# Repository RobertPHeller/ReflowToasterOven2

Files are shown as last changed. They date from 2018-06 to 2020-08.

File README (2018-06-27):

This project is based on the Instructables "Hack a Toaster Oven for Reflow
Soldering" by frank26080115 at
https://www.instructables.com/id/Hack-a-Toaster-Oven-for-Reflow-Soldering/

Notable differences:

1) It uses an Adafruit Feather M0 Expressas the processing element and all of
the electronics (except the display, pushbuttons, buzzer, and relay) are
mounted on an cut down BusBoard Prototype Systems BR1 solderable breadboard --
all of the components are through-hole components.

There is a KiCAD project here. It includes a "four layer" board. Actually I
have no intention of creating a "four layer" PCB. I intend to build this on
aBusBoard Prototype Systems BR1 solderable breadboard. The PCB I "designed"
with KiCAD is a mock up for the BR1 solderable breadboard. The green layer
represent the wiring already on the BR1 solderable breadboard, and includes
the bus strips. The red, blue and white "layers" represent the added wiring.
The board also provides the component placement. For those people without
KiCAD installed, I have included a PDF of the schematic in the file
ReflowToasterOven2.pdf and a SVG file of the board showing the layout.

2) Everything is mounted in a pair of plastic boxes and instead of "hacking"
an extension code, an AC power entry module and a pair of AC Receptacles are
used.

There are three files related to the mechanical construction:

ReflowToasterOven-mech2.tcl
ReflowToasterOven-mech2.gcad
ReflowToasterOven-mech2.dxf

ReflowToasterOven-mech2.tcl is a Tcl program that generates the 
ReflowToasterOven-mech2.gcad file, which is the input for the GCAD3D program.  
The ReflowToasterOven-mech2.dxf is a DXF file, that can be imported to any 3D 
cad program.

3) An Adafruit 1.8" *Color* TFT LCD SPI display is used, using Adafruit's 
graphics library.

4) The software is a "standard" Arduino project.

And the code lives in the ReflowToasterOven2 subdirectory. It compiles
successfully and just fits in the Uno's flash memory and only 1/2 of the SRAM
is used by static variables, leaving just under 1K for dynamic variables.

You will need to install the Adafruit ST7735 and Adafruit_GFX libraries from 
Adafruit's GitHub repo.  You will also need the MsTimer2 library 
(http://www.pjrc.com/teensy/td_libs_MsTimer2.html).

*Most* of the code is copied from the original program by frank26080115.  I 
modified things to use C++ classes and adapted to use the Arduino I/O 
libraries, the Adafruit ST7735-based TFT display and the MsTimer2 library.

I have not built or tested it yet.

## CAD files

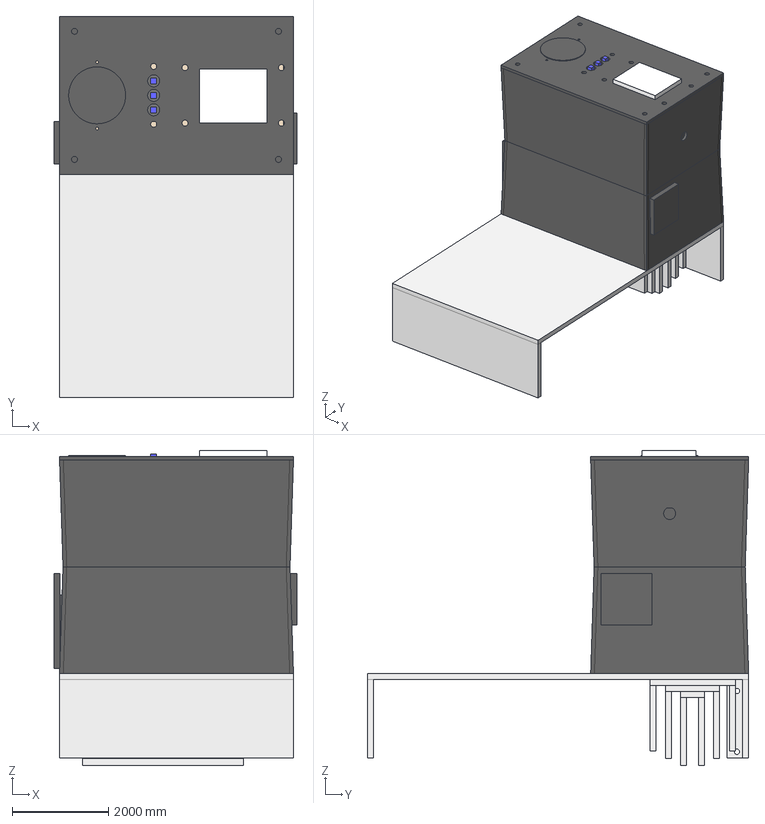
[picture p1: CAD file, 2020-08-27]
ReflowToasterOven.fcstd
5036.1 x 7910.9 x 6534.9 mm
reflowcontrol_upperbox
reflowcontrol_upperbox_lid
reflowcontrol_lowerbox
reflowcontrol_board_board
reflowcontrol_board_h1
reflowcontrol_board_h2
reflowcontrol_board_feather
reflowcontrol_board_usbjack
reflowcontrol_display_board
reflowcontrol_display_display
reflowcontrol_buzzer
reflowcontrol_relay
reflowcontrol_acpowerentry
reflowcontrol_backrecept
reflowcontrol_heatsink_mainpanel
reflowcontrol_heatsink_fin1
reflowcontrol_heatsink_fin2
reflowcontrol_heatsink_fin3
reflowcontrol_buttonboard_board
reflowcontrol_buttonboard_button1_body
reflowcontrol_buttonboard_button1_button
reflowcontrol_buttonboard_button2_body
reflowcontrol_buttonboard_button2_button
reflowcontrol_buttonboard_button3_body
reflowcontrol_buttonboard_button3_button
reflowcontrol_board_standoff1
reflowcontrol_board_standoff2
reflowcontrol_board_standoff3
reflowcontrol_board_standoff4

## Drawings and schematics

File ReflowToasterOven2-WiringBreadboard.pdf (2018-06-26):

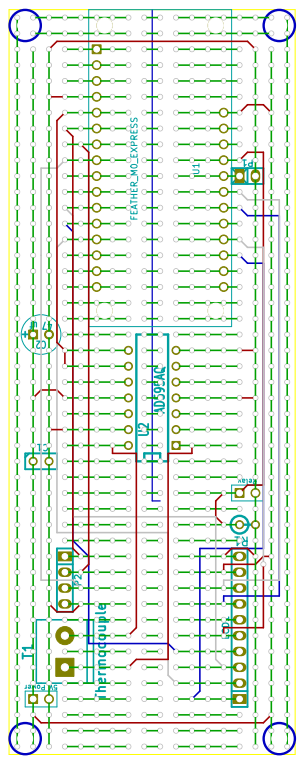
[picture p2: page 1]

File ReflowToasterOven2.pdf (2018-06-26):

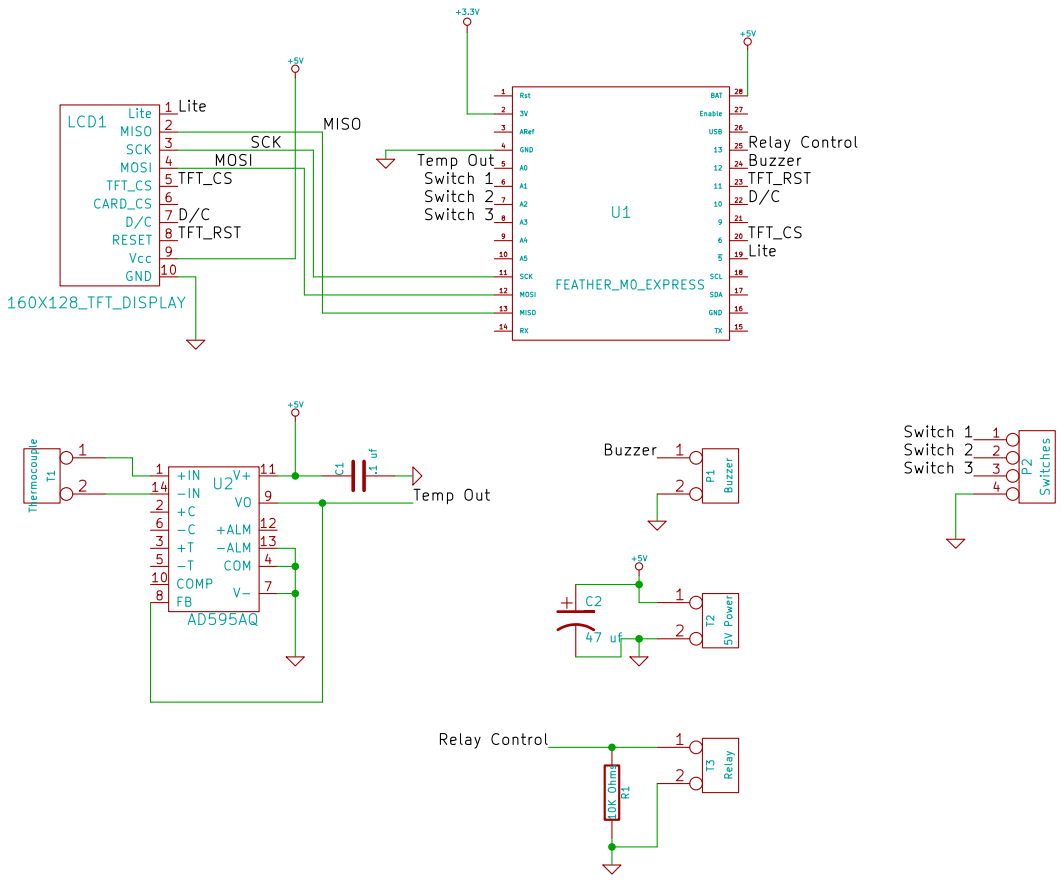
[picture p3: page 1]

Id: 1/1 Title: File: ReflowToasterOven2.sch
Sheet: /

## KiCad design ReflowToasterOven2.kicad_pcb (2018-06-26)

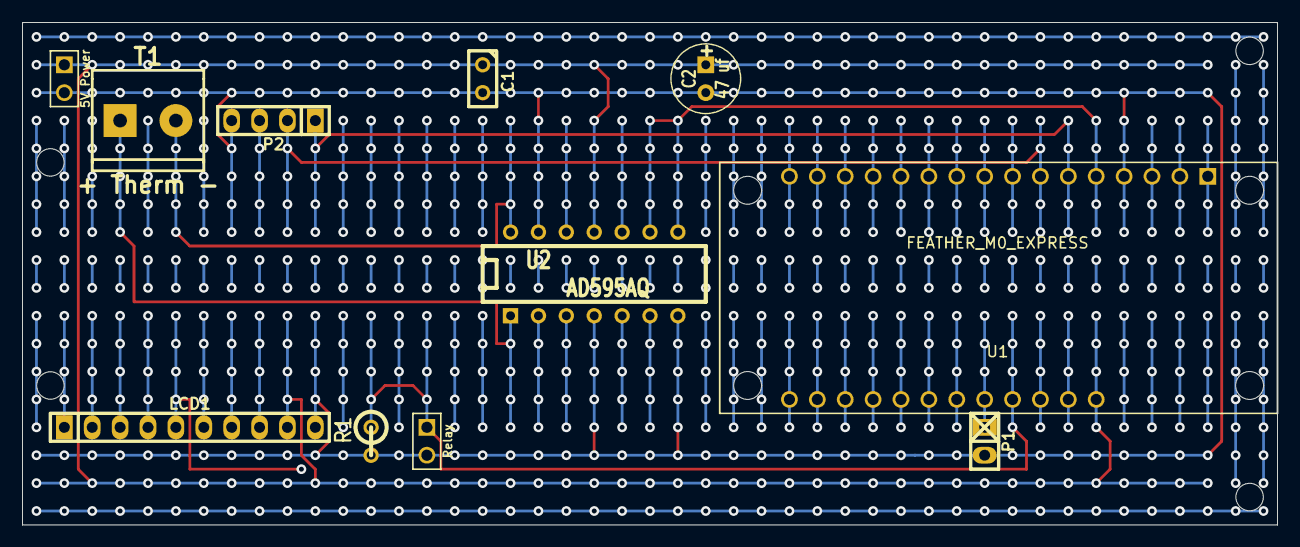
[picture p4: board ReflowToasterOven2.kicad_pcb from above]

Board: 4 copper layers, 114.3 x 45.8 mm, 15 parts (0 on the bottom side), 17 nets.

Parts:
C1: .1 uf; C1
C2: 47 uf; C1V7
LCD1: 160X128_TFT_DISPLAY; pin_strip_10
MH: MountingHole_2-5mm_RevA_Date21Jun2010
MH#2, MH#3, MH#4: MountingHole_2-5mm_RevA_Date21Jun2010
P1: Buzzer; pin_strip_2
P2: Switches; pin_strip_4
R1: 10K Ohms; R1
T1: + Therm -; mors_2p
T2: 5V Power; ScrewTerm2.54-2
T3: Relay; ScrewTerm2.54-2
U1: FEATHER_M0_EXPRESS; AdafruitFeather
U2: AD595AQ; DIP-14__300

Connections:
+5V: C1.1, C2.1, LCD1.9, T2.1, U1.28, U2.11
/Buzzer: P1.1, U1.24
/D/C: LCD1.7, U1.22
/Lite: LCD1.1, U1.19
/MISO: LCD1.2, U1.13
/MOSI: LCD1.4, U1.12
/Relay Control: R1.1, T3.1, U1.25
/SCK: LCD1.3, U1.11
/Switch 1: P2.1, U1.6
/Switch 2: P2.2, U1.7
/Switch 3: P2.3, U1.8
/TFT_CS: LCD1.5, U1.20
/TFT_RST: LCD1.8, U1.23
/Temp Out: U1.5, U2.8, U2.9
GND: C1.2, C2.2, LCD1.10, P1.2, P2.4, R1.2, T2.2, T3.2, U1.4, U2.4, U2.7, U2.13
unnamed: T1.1, U2.1
unnamed: T1.2, U2.14

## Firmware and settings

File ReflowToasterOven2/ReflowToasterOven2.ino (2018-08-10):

// -!- C++ -!- //////////////////////////////////////////////////////////////
//
//  System        : 
//  Module        : 
//  Object Name   : $RCSfile$
//  Revision      : $Revision$
//  Date          : $Date$
//  Author        : $Author$
//  Created By    : Robert Heller
//  Created       : Sun Jun 24 09:38:54 2018
//  Last Modified : <180810.0919>
//
//  Description	
//
//  Notes
//
//  History
//	
/////////////////////////////////////////////////////////////////////////////
//
//    Copyright (C) 2018  Robert Heller D/B/A Deepwoods Software
//			51 Locke Hill Road
//			Wendell, MA 01379-9728
//
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
// 
//
//////////////////////////////////////////////////////////////////////////////
#include <Arduino.h>
#include <stdio.h>
//#include <EEPROM.h>

#include <Adafruit_GFX.h>
#include <Adafruit_ST7735.h>
#include <SPI.h>
#include <Adafruit_SPIFlash.h>
#include <Adafruit_SPIFlash_FatFs.h>
#include <Adafruit_ZeroTimer.h>
#include "reflowtoasteroven.h"
#include "temperaturemeasurement.h"
#include "heatingelement.h"
#include "Menu.h"
#include "FileIO.h"
#include "pitches.h"

static const char rcsid[] = "@(#) : $Id$";

settings_t settings; // store this globally so it's easy to access

FileIO filesystem;

void tmr_init();

Adafruit_ZeroTimer zt4 = Adafruit_ZeroTimer(4);


Menu menu = Menu();
TemperatureMeasurement sensor = TemperatureMeasurement();
Heat element = Heat();

void setup()
{
    Serial.begin(115200);
    Serial.println("Initializing...");
    
    filesystem.begin();
    sensor.init();
    element.init();
#ifdef TIMER
    tmr_init();
#endif
    menu.init();
    Serial.println("Reflow Toaster Oven 1.0 Setup finished");
    menu.main();
}

volatile uint16_t tmr_ovf_cnt = 0;
volatile char tmr_checktemp_flag = 0;
volatile char tmr_drawlcd_flag = 0;
volatile char tmr_writelog_flag = 0;

void loop() {
    if (Serial.available() > 0) {
        while (Serial.available() > 0 && Serial.read() != '\n') ;
        Serial.print("*** tmr_ovf_cnt = ");Serial.println(tmr_ovf_cnt);
        Serial.print("*** tmr_checktemp_flag = ");Serial.println(tmr_checktemp_flag);
        Serial.print("*** tmr_drawlcd_flag = ");Serial.println(tmr_drawlcd_flag);
        Serial.print("*** tmr_writelog_flag = ");Serial.println(tmr_writelog_flag);
        //menu.fillRect(0,0,50,50,ST7735_BLUE);
        //tone(BUZZER,NOTE_GS3,3000);
        delay(1000);
    } else {
        //menu.fillRect(25,25,25,24,ST7735_RED);
    }
#if 0
    if (button_up()) {
        button_debounce();
        while (button_up());
        button_debounce();
        Serial.println("Button up");
    } else if (button_mid()) {
        button_debounce();
        while (button_mid());
        button_debounce();
        Serial.println("Button mid");
    } else if (button_down()) {
        button_debounce();
        while (button_down());
        button_debounce();
        Serial.println("Button down");
    }
#endif
    delay(1);
} // Not used

void TIMER0_OVF_vect()
{
    element.isr();
    sensor.get_ADC_sample();
    
    tmr_ovf_cnt++;
    if (tmr_ovf_cnt % 1024 == 0) //  2s
    {
        tmr_ovf_cnt = 0;
        tmr_checktemp_flag = 1;
        tmr_drawlcd_flag = 1;
        tmr_writelog_flag = 1;
    }
    else if (tmr_ovf_cnt % 512 == 0) //  1s
    {
        tmr_checktemp_flag = 1;
        tmr_writelog_flag = 1;
    }
    else if (tmr_ovf_cnt % 256 == 0) //  0.5s
    {
        tmr_checktemp_flag = 1;
    }
}

void tmr_init()
{
    /********************* Timer #4, 8 bit, one callback with adjustable period */
    zt4.configure(TC_CLOCK_PRESCALER_DIV64, // prescaler: 48Mhz/64 = 750Khz
                  TC_COUNTER_SIZE_16BIT,   // bit width of timer/counter
                  TC_WAVE_GENERATION_MATCH_FREQ  // match style
                  );
    
    zt4.setPeriodMatch(1464, 1, 0); // 1 match, channel 0 -- 1.953125ms (512Hz == 750Khz/1464)
    zt4.setCallback(true, TC_CALLBACK_CC_CHANNEL0, TIMER0_OVF_vect); 
    zt4.enable(true);
}

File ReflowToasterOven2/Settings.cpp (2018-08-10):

// -!- C++ -!- //////////////////////////////////////////////////////////////
//
//  System        : 
//  Module        : 
//  Object Name   : $RCSfile$
//  Revision      : $Revision$
//  Date          : $Date$
//  Author        : $Author$
//  Created By    : Robert Heller
//  Created       : Sat Mar 24 15:41:16 2018
//  Last Modified : <180810.1114>
//
//  Description	
//
//  Notes
//
//  History
//	
/////////////////////////////////////////////////////////////////////////////
//
//    Copyright (C) 2018  Robert Heller D/B/A Deepwoods Software
//    (Portions Copyright (C) 2011 Frank Zhao)
//			51 Locke Hill Road
//			Wendell, MA 01379-9728
//
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
// 
//
//////////////////////////////////////////////////////////////////////////////

#include <Arduino.h>
#include "Settings.h"
#include <stdlib.h>
#include "dtostrg.h"

static const char rcsid[] = "@(#) : $Id$";

void Settings::Default() {
    pid_p = 6000.0;
    pid_i = 20.00;
    pid_d = -0.00;
    max_temp = 225.0;
    time_to_max = 300.0;
}

bool Settings::Valid() {
    return (max_temp > 0.0 && time_to_max > 0.0);
}

void Settings::Load() {
    if (!filesystem.begin()) return;
    // load the data block from EEPROM
    char *filebuffer,*p,*p2;
    File fp = fatfs.open("Settings.dat",FILE_READ);
    if (fp) {
        size_t len = fp.size();
        filebuffer = (char *)calloc(sizeof(char),len);
        fp.read(filebuffer,len);
        fp.close();
        p = filebuffer;
        pid_p = strtod(p,&p2);
        p = p2;
        while (*p && *p != '\n') p++;
        pid_i = strtod(p,&p2);
        p = p2;
        while (*p && *p != '\n') p++;
        pid_d = strtod(p,&p2);
        p = p2;
        while (*p && *p != '\n') p++;
        max_temp = strtod(p,&p2);
        p = p2;
        while (*p && *p != '\n') p++;
        time_to_max = strtod(p,&p2);
        p = p2;
        free(filebuffer);
        // verify data validity
        if (!Valid())  {
            // data not valid, reset to defaults
            Default();
            Save();
        }
    }
}

void Settings::Save() {
    //Serial.println("*** Settings::Save() entered");
    if (!filesystem.begin()) return;
    //Serial.println("*** Settings::Save(): after filesystem.begin()");
    // save the data block into EEPROM
    File fp = fatfs.open("Settings.dat",FILE_READ);
    if (fp) {
        fp.close();
        filesystem.DeleteFile("Settings.dat");
    }
    fp = fatfs.open("Settings.dat",FILE_WRITE);
    //Serial.println("*** Settings::Save(): file opened");
    if (fp) {
        static char buffer[16];
        dtostrg(pid_p,10,5,buffer);
        fp.write(buffer,strlen(buffer));fp.write("\n",1);
        dtostrg(pid_i,10,5,buffer);
        fp.write(buffer,strlen(buffer));fp.write("\n",1);
        dtostrg(pid_d,10,5,buffer);
        fp.write(buffer,strlen(buffer));fp.write("\n",1);
        dtostrg(max_temp,10,5,buffer);
        fp.write(buffer,strlen(buffer));fp.write("\n",1);
        dtostrg(time_to_max,10,5,buffer);
        fp.write(buffer,strlen(buffer));fp.write("\n",1);
        fp.close();
    }
}


void Settings::DownloadFromSerial()
{
    char LineBuffer[64],*p2;
    int line = 0;
    Serial.println("Settings?");
    while (1) {
        delay(100);
        int bytes = Serial.readBytesUntil('\n',LineBuffer,sizeof(LineBuffer));
        //Serial.print("*** Settings::DownloadFromSerial(): bytes = ");
        //Serial.println(bytes);
        if (bytes == 0) {
            if (line < 5) continue;
            else break;
        }
        line++;
        //Serial.print("*** Settings::DownloadFromSerial(): line = ");
        //Serial.println(line);
        switch (line) {
        case 1:
            pid_p = strtod(LineBuffer,&p2);
            break;
        case 2:
            pid_i = strtod(LineBuffer,&p2);
            break;
        case 3:
            pid_d = strtod(LineBuffer,&p2);
            break;
        case 4:
            max_temp = strtod(LineBuffer,&p2);
            break;
        case 5:
            time_to_max = strtod(LineBuffer,&p2);
            break;
        default:
            break;
        }
        Serial.println(line);
    }
    if (!Valid())  {
        Default();
        Save();
    }
}

void Settings::UploadToSerial()
{
    static char buffer[16];
    Serial.println("Settings>");
    dtostrg(pid_p,10,5,buffer);
    Serial.println(buffer);
    dtostrg(pid_i,10,5,buffer);
    Serial.println(buffer);
    dtostrg(pid_d,10,5,buffer);
    Serial.println(buffer);
    dtostrg(max_temp,10,5,buffer);
    Serial.println(buffer);
    dtostrg(time_to_max,10,5,buffer);
    Serial.println(buffer);
    Serial.println("Settings<");
}

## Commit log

2018-06-26 Initial Release
    [ReflowToasterOven2.kicad_pcb, ReflowToasterOven2.sch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]
2018-06-26 Label Update
    [ReflowToasterOven2.kicad_pcb, ReflowToasterOven2.sch]
2018-06-26 Fix file name typo
    [Profile.cpp]
2018-08-10 Ready for the actual toaster oven and final testing and calibration
2018-08-21 Update buildTC.sh for arm host (Raspi)
2020-08-26 Add Fritzing and FreeCAD files.
    [ButtonBoard.fzz, ReflowOven2.fzz, ReflowToasterOven.fcstd]
2020-08-27 Add Button Board.
    [ReflowToasterOven.fcstd]

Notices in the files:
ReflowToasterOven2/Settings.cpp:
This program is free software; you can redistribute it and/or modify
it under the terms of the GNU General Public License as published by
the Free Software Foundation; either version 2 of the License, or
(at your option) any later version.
